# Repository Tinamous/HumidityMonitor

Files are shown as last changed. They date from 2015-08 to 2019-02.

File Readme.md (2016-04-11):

3D Printer Filament Humidity Controlled Storage
===============================================

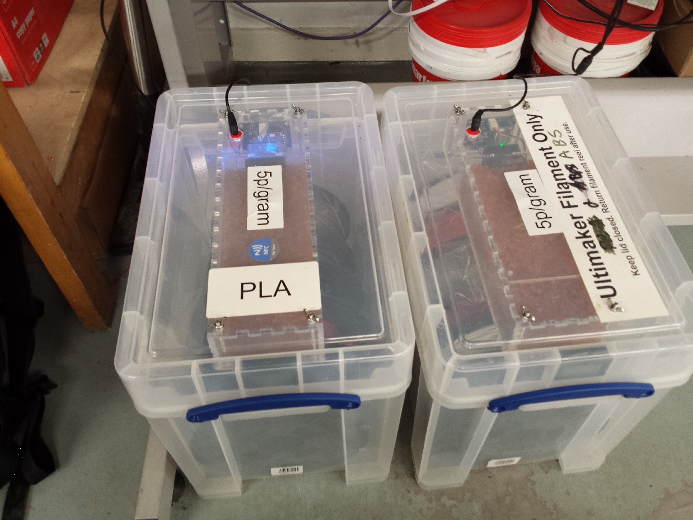
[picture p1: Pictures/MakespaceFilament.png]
Filament storage boxes in use


Comprises of:

* Outer box (19L XL Really Useful Box).
* Laser cut acrylic silica gel case
* Particle Photon based humidity sensing and fan control PCB inside silica gel case.
* Self indicating silica gel inside #2.

1) Outer box
---------------------
A 19L XL A4 suspension folder Really Useful Box works well. Be sure to get the one with the high lid. (not the regular 19L box).

* Needed: Staples link to case.
* Maplin: http://www.maplin.co.uk/p/really-useful-19l-xl-box-n68fl (Untested but it's a lot cheaper than the staples one!)

The lid of the 19L XL case will need to be drilled to hold the acrylic silica gel cartridge in place. Do this before gluing the cartridge so the acrylic can be used as a template.

Place what is labeled as the top piece in the designs (actually the bottom piece with all the holes in it) onto the lid and mark/drill the 4 corner screws.

If you wish for the power to go in via the top (prevents boxes being stacked but is obvious that it is powered so prevents people missing it) use the large bottom piece (actually top) with the larger round hole in it and align the two corner screws then drill out the larger hole in the lid.

Power connectors were sourced from eBay (http://www.ebay.co.uk/itm/PLUGZ2GO-2-1MM-X-5-5MM-PANEL-MOUNT-DC-PLUG-SOCKET-JACK-CHOICE-OF-COLOUR-/221456273750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), be sure you can get the same before drilling the power connector hole in the lid. 

Alternativly power connection may be done from the side of the lid by running the power cable out of either top or bottom gel case holes, this would allow the boxes to be stacked, although it makes it less obvious theirs a cable connected so care needs to be taken.

M4 x 70mm machine screws with washer+wingnut on the lit are used to hold the actylic case to the lid. (See notes below on re-filling the silica gel)

2) Laser Cut Acrylic Gel Case
-----------------------------
5mm clear acrylic cut as detailed in Hardware\Case\LaserCut

(You can use another colour obviously but the clear is cheaper and allows the self indicating gel to be seen).

The case contains a 40mm fan. A standard 3 pin PC fan should be used with a filter to prevent silica gel getting in to it.

3) Humidity Monitor.
---------------------

Use Particle Photon (or can use Particle Core device).

See Hardware\PCB\V2

Don't use V1 as the FET has Source/Drain the wrong way around.

PCB available from OSHPark: https://oshpark.com/shared_projects/nOVDuNCE

JP3 or JP4 are used for the HTU21 sensor. SparkFun and eBay boards have swapped SDA/SCL, watch for correct version.
* JP3 is for the eBay version
* JP4 is for SparkFun version.

Build using build.particle.io, see source folder.

A 12V power supply us needed capable of supplying upto 500mA (depends on the fan).

If a 5V fan is used a 5V PSU can be used and the onboard regulator not fitted, instead connecting the Vin to VOut holes with a piece of wire.

The PCB is mounted to the case with 4x 10mm plastic standoffs and 8x M3x8mm bolts from either side.

4) Self indicating silica gel
-----------------------------
Almost any silica gel can be used and doesn't need to be self indicating but it helps with seeing when the gel needs to be dried and when drying the gel that it is ready.

Gel should be stored in a sealed box/bag when not in use.

Gel can be re-generated by heating in an electric (untested on gas) oven for about 3 hours at 110°C

5) Connection to Tinamous
-------------------------
Optional step. Tinamous supports Particle devices by use of the ParticleBot in Tinamous and will automatically bring in and store devices/measurements so the humidity can be remotely monitored.

PLA Filament storage 24 hour humdity chart:

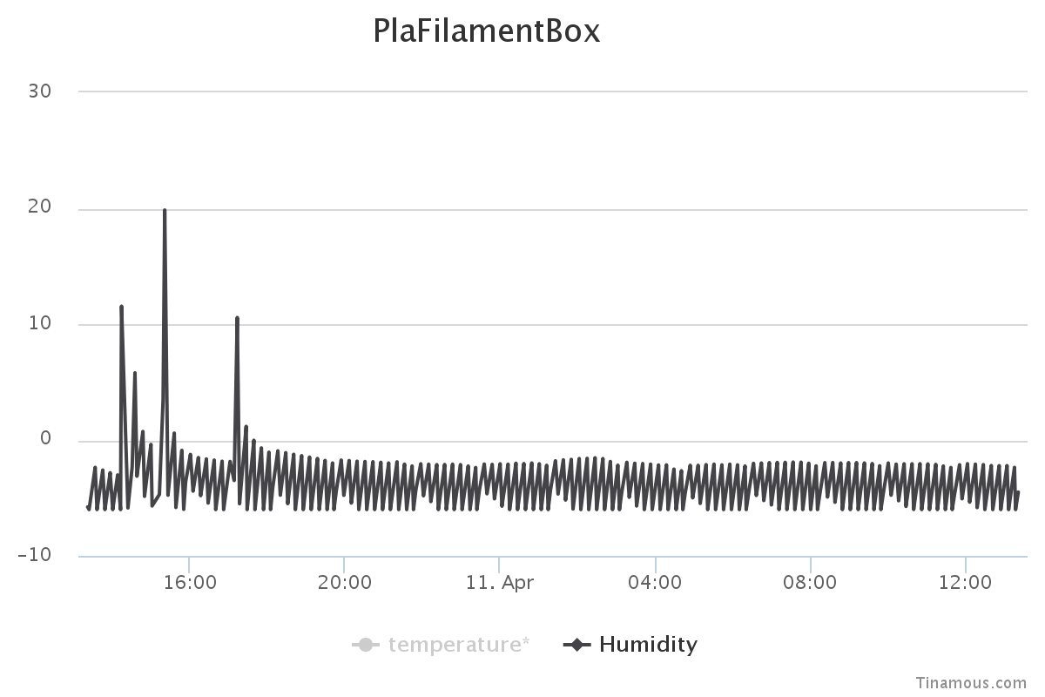
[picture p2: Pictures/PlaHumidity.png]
Humidity last 24 hours


PLA Filament storage 7 day humidity chart with change of gel:

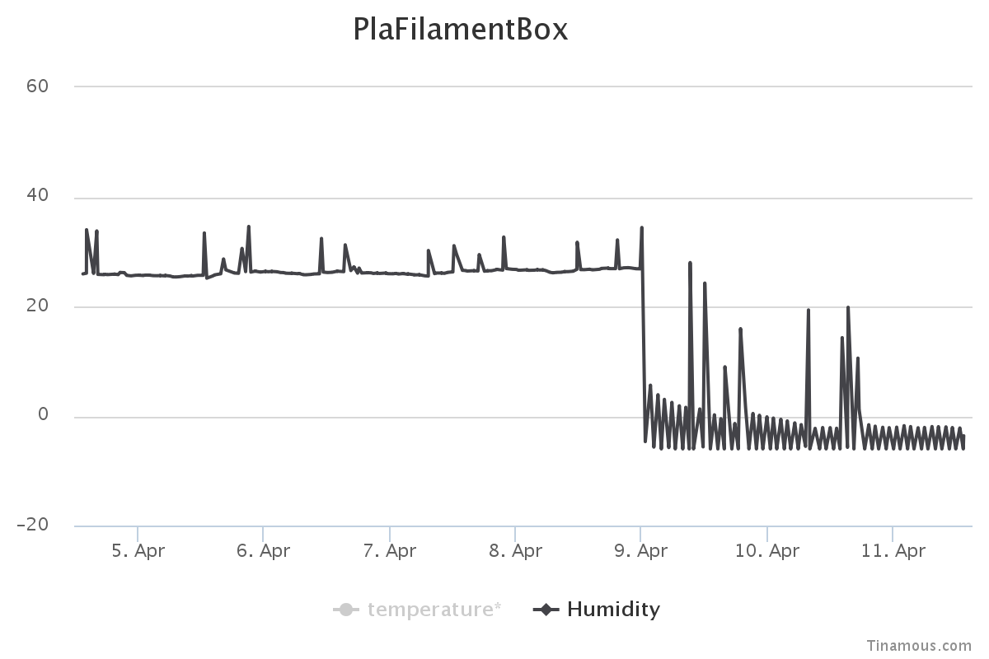
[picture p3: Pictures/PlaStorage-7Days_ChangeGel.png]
Humidity last 7 days


Notes
=====

Replacing the silica gel.
--------------------------

This needs to be done regularly (depending on usage), ca. every month and the silica gel dried (110C 3hrs spread out on a baking tray). I typically replace when it gets to about 20% humidity in the box.

The silica gel can be dried and re-used.

Silica gel will try to go everywhere.

* Remove acrylic case from box lid (place on flat surface, undo wing nuts on top of box.
* Remove lid upwards leaving acrylic case on flat surface.
* Replace 2x win nuts onto acrylic case at PCB end to hold the large top piece in place
* Remove small top piece from top to expose silica gel
* Remove 2x screws that were holding the top peice in
** failure to remove these now will result in silica gel getting wedged behind them and stopping correct alignment.
* Pour gel into a container (suggest Sistem 2.35L tub - http://www.amazon.co.uk/gp/product/B005D6Y4IA?psc=1&redirect=true&ref_=oh_aui_detailpage_o03_s00)
* Put funnel into opening
* Slowly pour fresh silica gel into acrylic case, shaking to move the gel down the case as you go
* Do not fill completly full, allow 1/2-1 inch space when the case is closed up and stood tall 
* Re-Fit small lid peiece
* Holding top in place, stand case tall to allow silica gel to fully move down to the fan and make re-fitting screws easier.
* Refit 2x screws for the small lid piece.
* Stand back down, remove 2x wingnuts to allow lit to be fitted.
* Fit box lit and re-fit wing nuts.

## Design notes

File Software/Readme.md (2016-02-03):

Humidity Monitor Source
-----------------------

Build and deployed using build.particle.io

If you paste this into a new file at build.particle.io you will need to manually add the HTU21D library (from the libraries tab).

Watch for the hardware version used. You should be using 0.2 PCB (i.e. Version 2), ensure version 1 pin assignments are commented out.

This application publishes senml messages which are automatically picked up by Tinamous.com to record the humidity/temperature levels and Status messages which show on the timeline.

Note that setting a new fan humidity trigger level using setFanOnAt method (which sets fanOnAtHumidityLevel) remotely does not persist this, it will be lost on power cycle/reset.

The application monitors the humidity level and will run the fan as needed.
* Either every n seconds (10s loop * 60, fan runs for 120s).
* When humidity > fanOnAtHumidityLevel (20%) and < 40% - fan will run for 120s or as long as the humidity level remains in this zone.
* If humidity level > 40% the fan is stopped to prevent flooding the silica gel with moisture (it is assumed to be in open air).

The Photon has a RGB LED on top, the color or this is used to indicate humidity levels
* Red - Humidity > 30%
* Yellow - Humidity > 20%
* Green - Humidity <= 20%

The fan can be remotely controlled via the Particle API (and via Tinamous) using:
* fanOn - runs the fan for 10 minutes
* fanOff - stops the fan within 10 seconds

No power saving is attempted with this version. A 10 second delay happens every loop which would be a good time to switch the WiFi off, however this makes updating and controlling the unit difficult and as it uses external power their is little need for power saving.

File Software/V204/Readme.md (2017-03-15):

Humidity Monitor Source
-----------------------

Build and deployed using build.particle.io

Paste the code from Humidityv4.ino into a new file at build.particle.io you will need to manually add the HTU21D library (from the libraries tab).

This works with the V2.04 PCB

This application publishes senml messages which are automatically picked up by Tinamous.com to record the humidity/temperature levels and Status messages which show on the timeline.

The application monitors the humidity level and will run the fan as needed.
* Either every n seconds (10s loop * 60, fan runs for 20s).
* When humidity > fanOnAtHumidityLevel (20%) and < humidityWarningLevel (30%) - fan will run for 60s or as long as the humidity level remains in this zone.
* If humidity level > humidityWarningLevel (30%) the fan is stopped and the beeper sounded to prevent flooding the silica gel with moisture (it is assumed to be in open air).

The Photon has a RGB LED on top, the color or this is used to indicate humidity levels
* Red - Humidity > 30%
* Yellow - Humidity > 20%
* Green - Humidity <= 20%

The fan can be remotely controlled via the Particle API (and via Tinamous) using:
* fanOn - runs the fan for 10 minutes
* fanOff - stops the fan within 10 seconds

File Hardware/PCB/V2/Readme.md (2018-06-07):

Filament Box IoT Humidity Sense and Control
---------------------------------------------

Used to monitor the humidity level in a 3D filament storage box and re-circulate the air through a silica gel cartridge.

Notes:
* 7805 Regulator should be replaces with a switching "780x replacement" type device to keep heat down. The 7805 will get very hot dropping 12v to 5v.
* JP3 and 4 are variants of connectors for HTU21D breakout boards.
** JP4 should be used with the Spark Fun version (https://www.sparkfun.com/products/12064)
** JP3 should be used with the common eBay version (SDA/SCL swapped from Spark Fun version).
* Normal use is intended for 12V with a 12V fan. However if using a 5V fan the supply may be dropped to 5V and IC1 (7805) not fitted, instead pads 1 & 3 connected to feed 5V directly into the photo's 5V supply pin.
* Do not use photon USB B connector to provide 5V for fan, it will not supply the full 5v and may not have PCB traces strong enough for the fan current.

Untested at this time. Awaiting PCBs.

BOM:

All 0805 unless specified

F1 - Fuse Farnell 1822224

D1,D2 - IN4148W (2x)
D4 - MBRA140
D3 - Green Reverse LED
D7 - Red Reverse LED
D8 - Yellow Reverse LED

R1,R2 - 10k (2x)
R3 - 100k
R4 - 180R
R5,R6,R7 - 1k5 (3x)

Q1 - BC817
Q2 - NXP2301

C1 - 1.0uF 
C4 - 0.1 25V
C2,C5 - 0.1uF (x)

SG1 - Buzzer (Farnell: 2098836)

JP1 - 2 Pin Molex + Header + 2.1MM DC Jack 973-1148
JP2 - 3 Pin Moxel + 3 wire 40mm fan 9731156

IC1 - 7805 equivelant
JP3 - HTU21D equv
U3 - Photon (needs 2x 18Pin headers)

PCB Spacers (4x)
M3 Machine Screws (8x)

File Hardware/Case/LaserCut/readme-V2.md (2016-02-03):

This is a case for silica gel that is inside the filament case. 

It is powered to monitor the humidity level and to run a fan forcing the humid air over the silica gel which greatly improves the reduction in humidity.

All measurements are in mm and from outside edges.

Case designed with http://www.makercase.com/

Files:
* GelCase-V2.02.svg - master svg as generated by MakerCase. Do not use for cutting
* GelCase-V2.02.json - master MakerCase model.
* Sheet-1-V2.02 - Cutting.svg - svg used to generate dxf for cutting. Has better layout. Cut from 600mm x 400mm x 5mm acrylic.
* FanInsert-V2.02.svg - the fan insert to fit cutouts defined in the gel case. This holds a 40mm fan. Fan needs filter to prevent inflow of silica gel.

Use only these for cutting the acrylic.
* Sheet-1-V2.02 - Cutting.svg
* FanInsert-V2.02.svg

Notes:
* In MakerCase the top and bottom are transposed. This readme refers to "Bottom" and "Top" as they are references in MakerCase with (actually ...) added to point out the final 
* When loading the json file into MakerCase ("Load Model" button) the material thickness is not correctly reloaded - use "Custom Material Thickness" and set to 5mm.

Assembly:
*Case should be glued on all sides except 
** The bottom (actually top) - the 2 part long piece with round power hole and 6 mounting holes.
** The fan insert
* Tensol 12 should be used for gluing the acrylic.
* Refrigerate glue for 12 hours before use.
* Remove protective cover fom acrylic for all except the bottom (aka top).
* Use electrical tape to hold the pieces together when gluing.
* Allow 3-4 hours for the glue to set (watch for glue leaking through joint - clean up as needed - don't rest on paper towels as it sticks)
* You may wish to fit the bottom (aka top) whilst the glue sets to help keep the case square but be careful it isn't glued inadvertantly via the glue up the sides

Dimensions
-----------

Outside:
--------
Height: 60 
Width: 100
Length: 300

Top (actually bottom):
------

Vent holes.

x 10 to 90 every 10mm
y 90 to 290 every 10mm

Large air intake:
* 15,20 -> 85,70 (70x50 mm) (buts up to fan mount

Top/Bottom connector mounts

M4 holes. 8mm support for 3mm screw.
8/2 = 4mm offset for center.
12 mm from each corner.

* M4 10,10
* M4 90,10
- first section
* M4 10,240
* M4 90,240

* M4 10,290
* M4 90,290

Bottom (actually top):
-------
Do not glue to rest of cased. It is removable to allow PCB to be accessed and gel to be replaced.

Helpd in place by screws to fan assembly and side moning screws.

Holes to align with top holes for fan/PCB enclosure.

- first secotion
* M4 10,290
* M4 90,290
* M4 10,60
* M4 90,60
- second section
* M4 10,10
* M4 90,10

M4 - Fan case (Not used)
* 19,345 - 20
* 81,345 - 20
* 19,345 - 102,
* 81,345 - 102

{"params":[19,20,4,5],"type":"roundHole"},
{"params":[81,20,4,6],"type":"roundHole"},
{"params":[81,102,4,7],"type":"roundHole"},
{"params":[19,102,4,8],"type":"roundHole"},

Back:
-------
PCB mount:
* M4 @ 24,11
* M4 @ 24,49
* M4 @ 76,11
* M4 @ 76,49

Extra:
-------

Cut line at 245mm in bottom to allow small segment to be removed for easier emptying.

** Holes in tabs to allow for fixing of top and lower segment.

Internal partition
-------------------

M4 - Fan mount.
x,y,size, index
* {"params":[66,29,4,1],"type":"roundHole"},
* {"params":[34,29,4,2],"type":"roundHole"},
* {"params":[66,61,4,3],"type":"roundHole"},
* {"params":[34,61,4,4],"type":"roundHole"},

M4 - Fan case
* 19, 20
* 81,20
* 19,102,
* 81,102

{"params":[19,20,4,5],"type":"roundHole"},
{"params":[81,20,4,6],"type":"roundHole"},
{"params":[81,102,4,7],"type":"roundHole"},
{"params":[19,102,4,8],"type":"roundHole"},

// @ 25,95 25mm x 10mm - humidity sensor + power
{"params":[25,95,25, 25,10,9],"type":"rectHole"},

Fan
* {"params":[50,55,38,27],"type":"roundHole"}],

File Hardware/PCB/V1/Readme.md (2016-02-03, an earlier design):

Version 1 Design.

Note that the Q1 has Source and Drain pins the wrong way around. When fitting Q1 rotate it 180 degrees and shift right so that the gate pin is not over a hole and on the right hand side.

Connect a wire between gate and the left most hole for Q1 (from above with the photon on the right). remaining 2 pins go into the remaining holes.

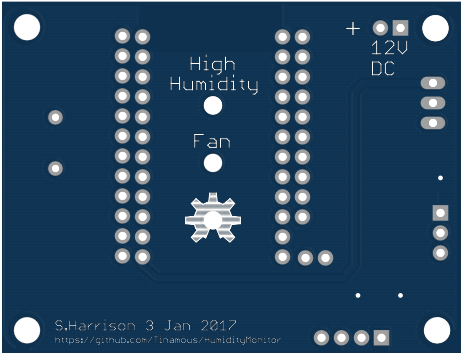
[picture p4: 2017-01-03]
Hardware/PCB/V2/Images/PcbBottom-V2.04.png

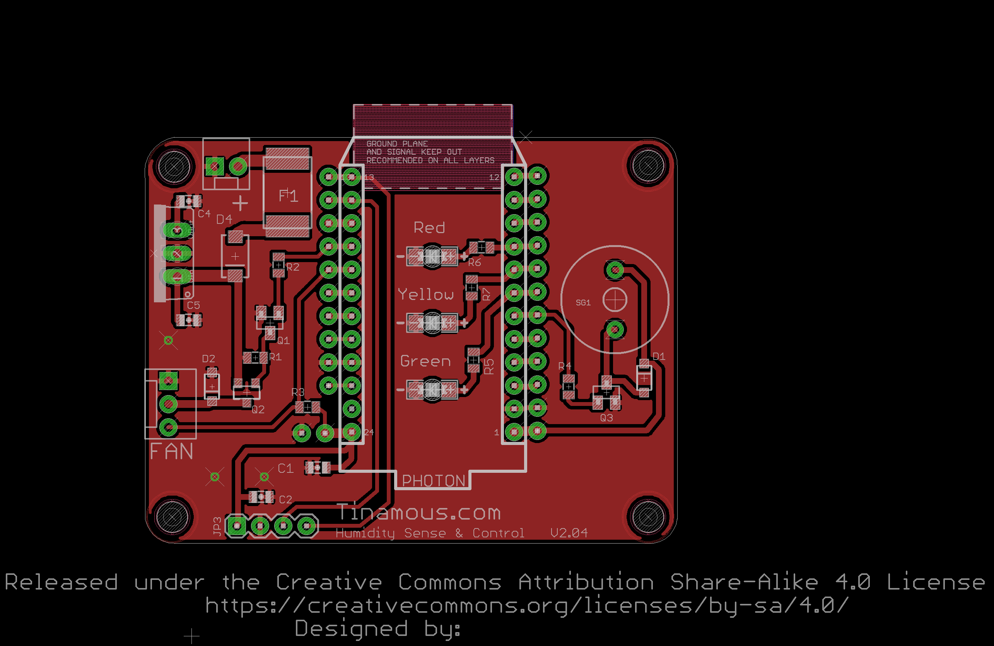
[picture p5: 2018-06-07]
Hardware/PCB/V2/Images/PcbTop-Design-V2.04.png

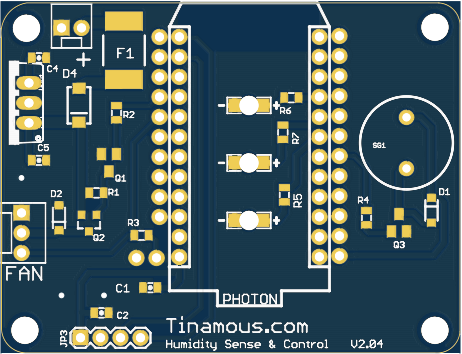
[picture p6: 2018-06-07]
Hardware/PCB/V2/Images/PcbTop-V2.04b.png

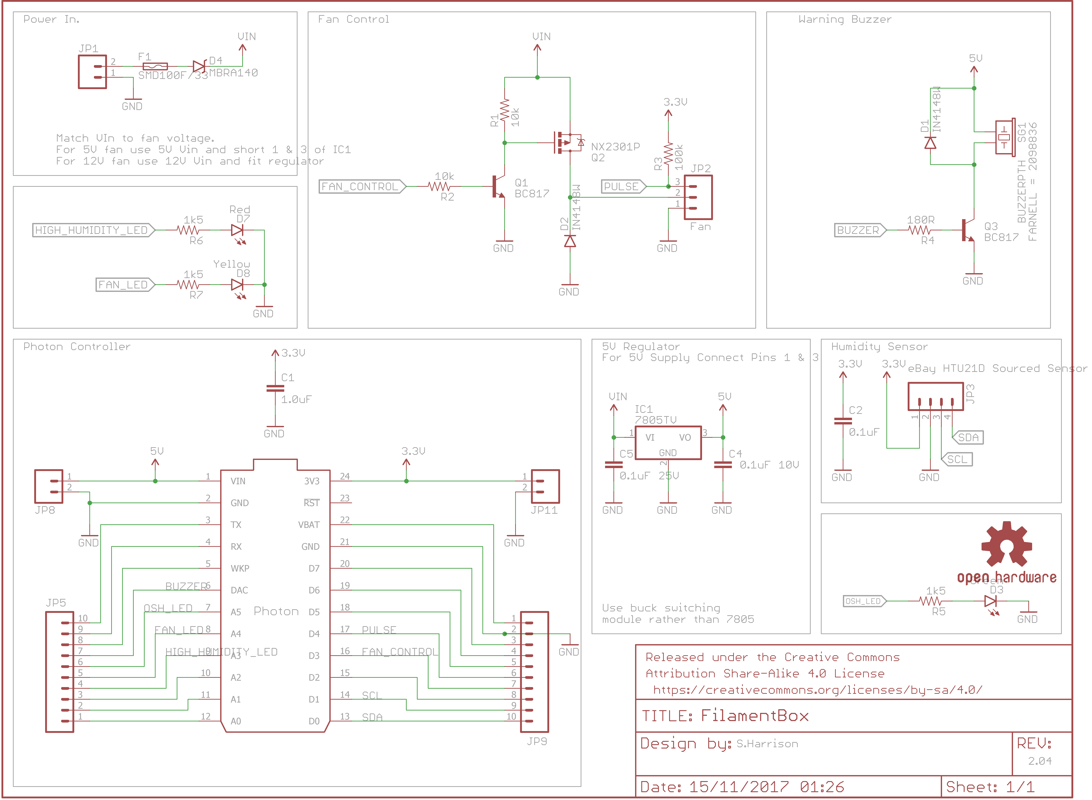
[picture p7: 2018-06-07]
Hardware/PCB/V2/Images/Schematic-V2.04.png

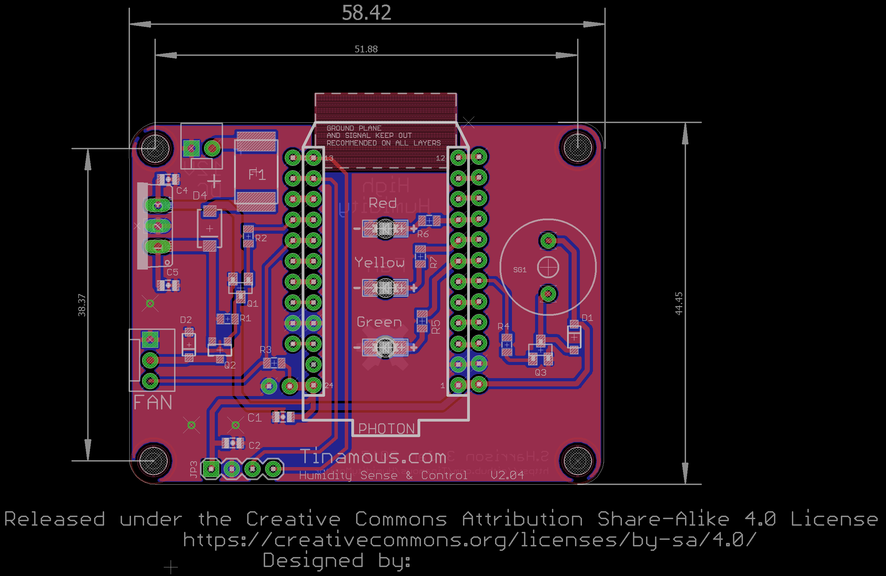
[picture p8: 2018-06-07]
Hardware/PCB/V2/Images/PCBAll-V2.04.png

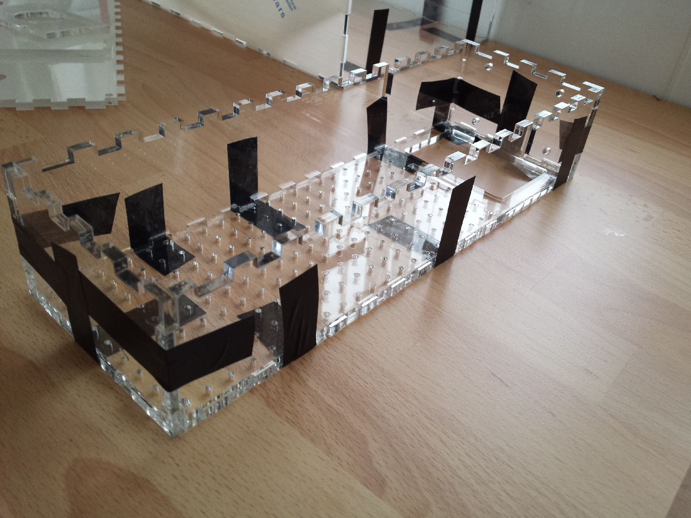
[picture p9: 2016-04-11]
Pictures/Gluing3.png

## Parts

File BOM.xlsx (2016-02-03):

Component | Part | Size/Value | Qty | Part Number(s) | Supplier | Supplier Part | Cost | Alt. Supplier | Alt. Supplier Part | Notes
Overall:
 | Really Useful Box | 19L XL | 1 |  | Staples | http://www.staples.co.uk/plastic-storage/cbs/431832.html?promoCode=200200555&Effort_Code=WW&Find_Number=431832 | 17.99 | Maplin | http://www.maplin.co.uk/p/really-useful-19l-xl-box-n68fl
 | Sistem tub | 2.35L | 1 |  | Amazon.co.uk | http://www.amazon.co.uk/gp/product/B005D6Y4IA?psc=1&redirect=true&ref_=oh_aui_detailpage_o03_s00 | 5.5 |  |  | Unused gel storage
 | 12V PSU |  | 1 |  | Maplin | N93JU | 9.99 |  |  | http://www.maplin.co.uk/p/12v-500ma-acdc-power-supply-n93ju
 | Machine Screw | M4 x 70mm | 4 |  | Westfield Fastners | http://www.westfieldfasteners.co.uk/A2_ScrewBolt_PoziPan_M4.html | 2.47
 | Wing nut | M4 | 4 |  | Westfield Fastners | http://www.westfieldfasteners.co.uk/A2_Nut_M4.html | 3.29
 | Draft Excluder |  | 1pk |  | B&Q |  |  | Wickes
 | Fan | 40mm | 1 |  | Maplin | N86QQ | 5 | http://www.maplin.co.uk/p/40mm-brushless-12vdc-axial-fan-yz41u
 | Fan filter | 40mm | 1 |  | eBay | http://www.ebay.co.uk/itm/like/291536178882 | 1.73
 | Silica Gel | 1kg | 1 |  | eBay | http://www.ebay.co.uk/itm/1000g-1kg-BONUS-100g-BAG-Silica-Gel-Desiccant-Self-Indicating-Loose-/111737656127 | 8.95
 | M3 Bolts | M3 x 25mm | 4 |  |  |  |  |  |  | Select length based on fan depth + 5mm + grill
 | M3 Nuts | M3 | 4
Acrylic Case: |  |  | QTY
 | Acrylic Sheet | 600x400x5mm | 1 |  | http://plasticonline.co.uk/ | http://plasticonline.co.uk/acrylic/acrylic-sheets-1/clear-cast-acrylic-sheet-gs.html | 10.43 |  |  | Clear Cast Acrylic Sheet (GS) - 5mm - 600x400
 | Glue - Tensol 12 | 50ml | 1 |  |  | http://www.ebay.co.uk/itm/50ml-TENSOL-12-Bottle-ACRYLIC-Perspex-Bonding-Cement-Adhesive-Glue-/160652606560 | 5.35
PCB:
 | PCB |  |  | 1 | OSH Park | https://oshpark.com/shared_projects/nOVDuNCE | 15 |  |  | USD 20 - for 3.
 | Photon | With Headers |  | U3 | Particle | https://store.particle.io/collections/photon | 19.98 | CoolComponents.co.uk | https://www.coolcomponents.co.uk/photon-wi-fi-development-board.html
 | Photon Socket | 12Pin | 2 | U3 (Optional) | eBay | http://www.ebay.co.uk/itm/350800310361 | 1.69 |  |  | 2.54mm Single Row Female Pitch Header Socket Connector Pin Strip
 | Ceramic 0805 Cap | 0.1uF | 1 | C2 | Farnell | 1856422 | 0.04
 | Ceramic 0805 Cap | 1uF | 2 | C1,C4 | Farnell | 175-9422 | 0.066
 | Electrolytic - Through Hole | 10uF | 1 | C3 | Farnell
 | 5 V regulator (Use 7805 switching replacement) | 7805 | 1 | IC1 | eBay | http://www.ebay.co.uk/itm/331681032438 | 1.83
 | 2 Pin Molex 2.54mm pin | 2 pin | 1 | JP1 | Farnell | 9731148 | 0.084
 | 2 Pin Molex 2.54mm housing | 2 pin | 1 | JP1 | Farnell | 143126 | 0.135
 | Molex KK series crimp |  | 2 | JP1 | Farnell | 2424111 | 0.044 |  |  | Min. order 100
 | Thick film 0805 resistor | 10k | 2 | R1,R2 | Farnell
 | Thick film 0805 resistor | 100k | 1 | R3 | Farnell
 | BC817 Transistor (SOT23) | BC817 | 1 | Q1 | Farnell | 1081225 | 0.03
 | NX2301P P-Channel FET | NX2301P | 1 | Q2 | Farnell | 1894738 | 0.14
 | 3 Pin Molex 2.54mm | 3 Pin | 1 | JP2 | Farnell | 9731156 | 0.174
Do No Fit | Buzzer |  |  | SG1 | Farnell
Do No Fit | BC817 | BC817 | 1 | Q3 | Farnell | 1081225
Do No Fit | Thick film 0805 resistor | 180R | 1 | R4 | Farnell
 | HTU21D Breakout | HTU21D Breakout | 1 |  | eBay | http://www.ebay.co.uk/itm/1PC-NEW-HTU21D-Temperature-Humidity-Sensor-Breakout-Board-New-Module-/271969988766 | 1.5
 | 2.54mm pitch pins |  | 4 |  |  |  |  |  |  | To mount HTU21D board
 | Panel Socket | 2.1mmx5.5mm | 1 |  | eBay | http://www.ebay.co.uk/itm/221456273750 | 2.49 |  |  | For 2
 | PCB Mounts | M3x10mm | 4 |  | eBay
 | M3 Screws | M3x8mm | 8 |  | Farnell | 1419987 | 1.87 |  |  | For pk 100
Total Cost |  |  |  |  |  |  | 115.773

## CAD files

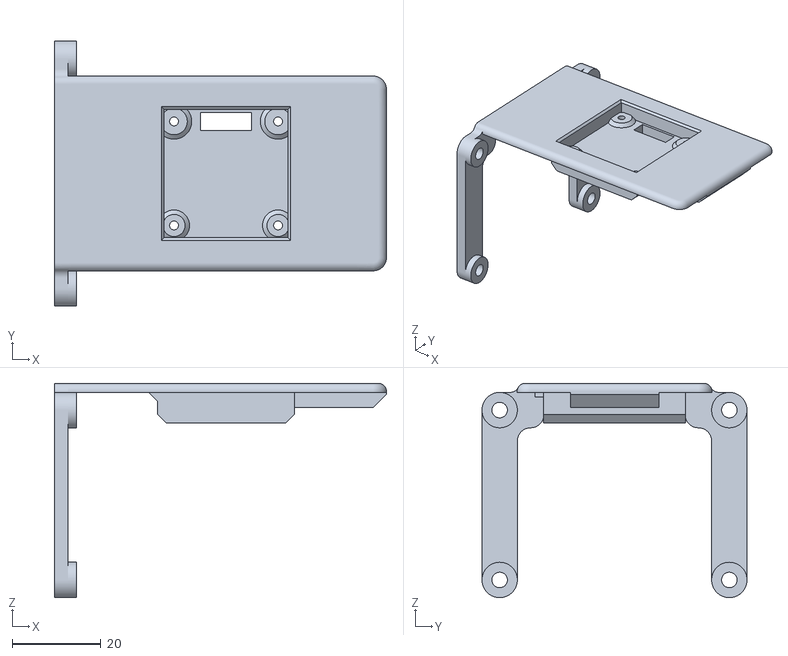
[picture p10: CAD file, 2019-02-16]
Hardware/Case/3D Printer/ScreehHolder2-4.stl
75.0 x 59.9 x 48.4

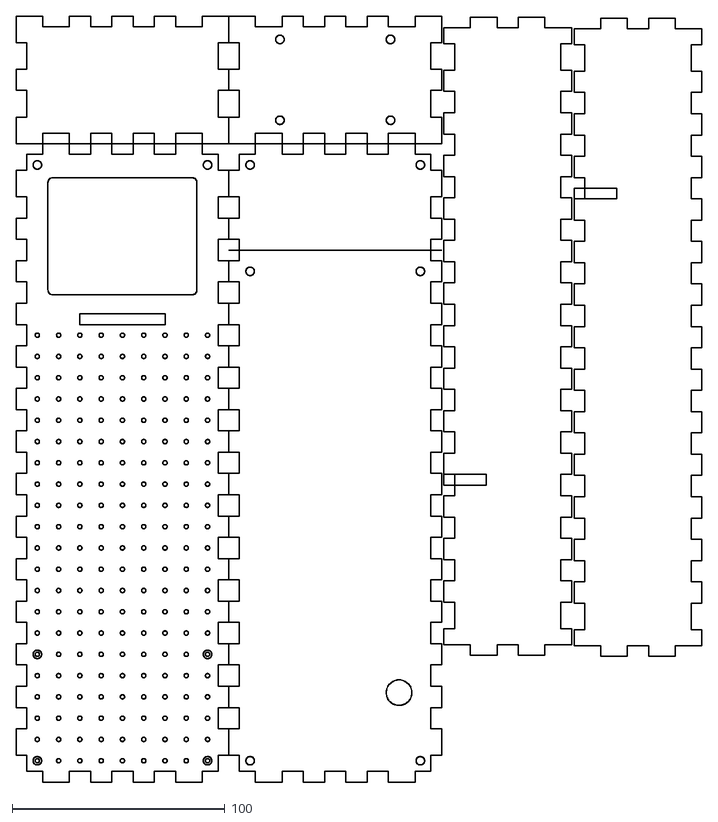
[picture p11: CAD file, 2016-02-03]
Hardware/Case/LaserCut/Sheet-1-V2.02 - Cutting.dxf
322.3 x 360.0

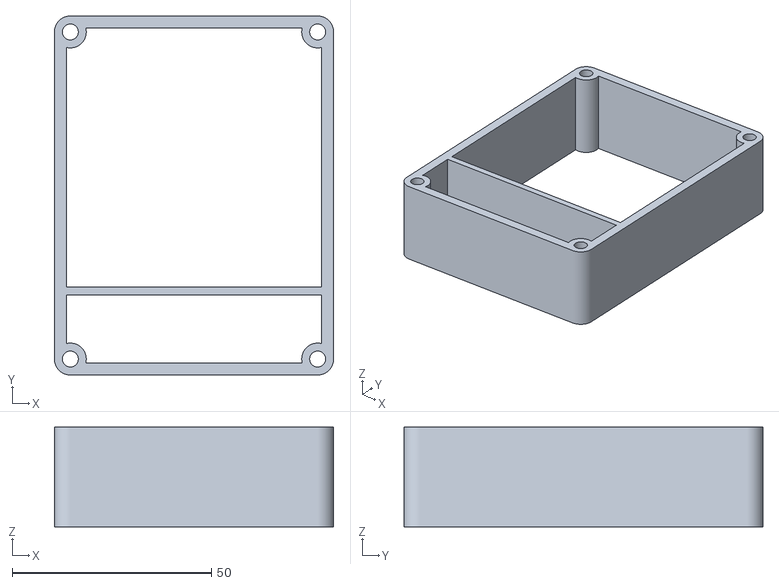
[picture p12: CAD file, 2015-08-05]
Hardware/Case/MiniGellBox/SilicaGelCase.stl
70.0 x 90.0 x 25.0

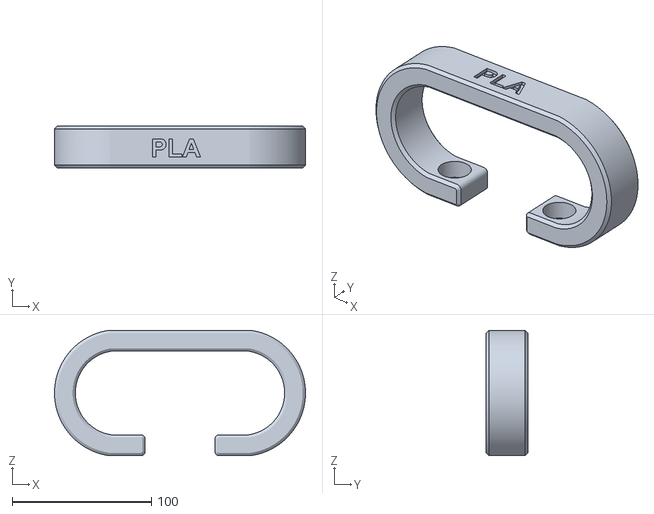
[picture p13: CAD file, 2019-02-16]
Hardware/Case/3D Printer/Handle3-PLA.stl
180.0 x 30.0 x 90.0

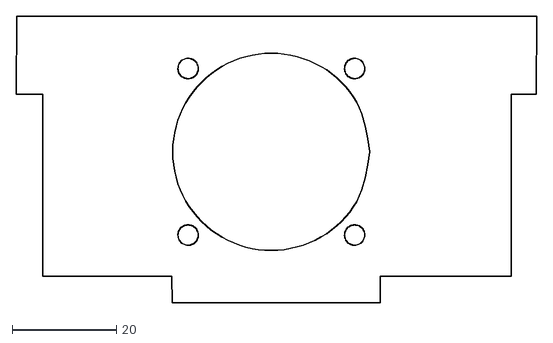
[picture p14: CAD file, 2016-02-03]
Hardware/Case/LaserCut/FanInsert-V2.02.dxf
100.0 x 55.1

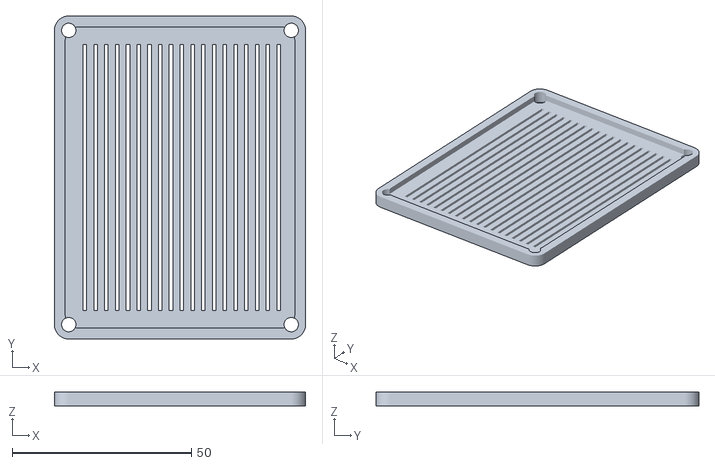
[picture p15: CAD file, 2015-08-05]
Hardware/Case/MiniGellBox/SilicaGelCaseLid.stl
70.0 x 90.0 x 4.00

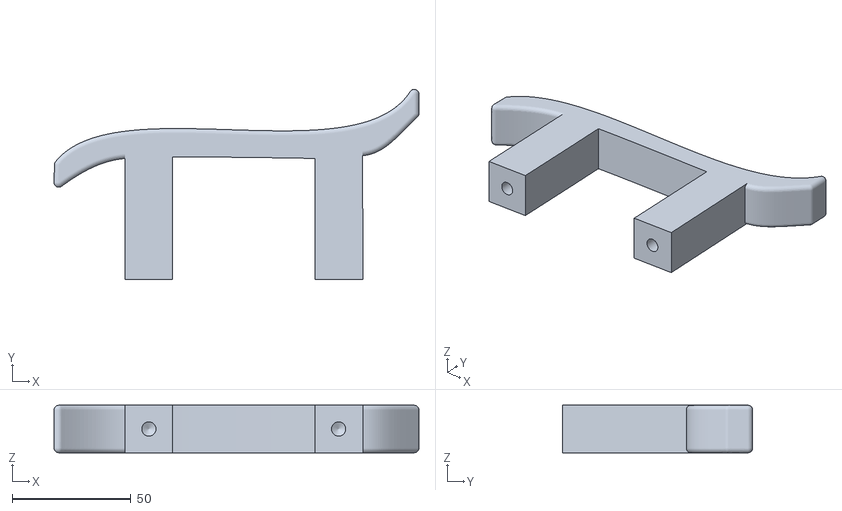
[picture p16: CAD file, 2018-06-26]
Hardware/Case/3D Printer/PiHandle.stl
153.5 x 80.1 x 20.0

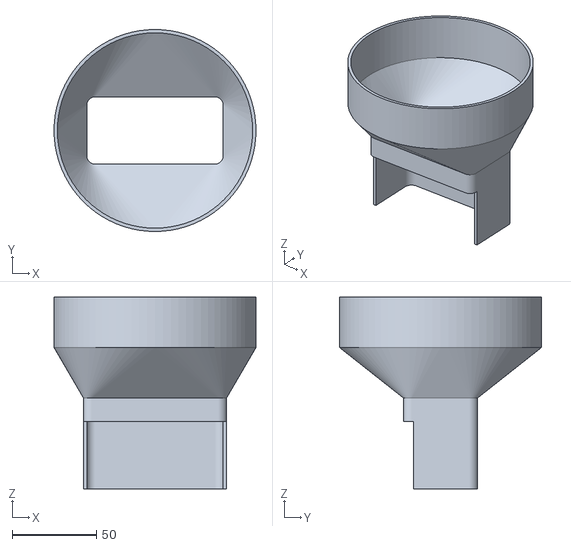
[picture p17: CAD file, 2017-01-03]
Hardware/Case/3D Printer/Funnel3.stl
120.0 x 120.0 x 114.0

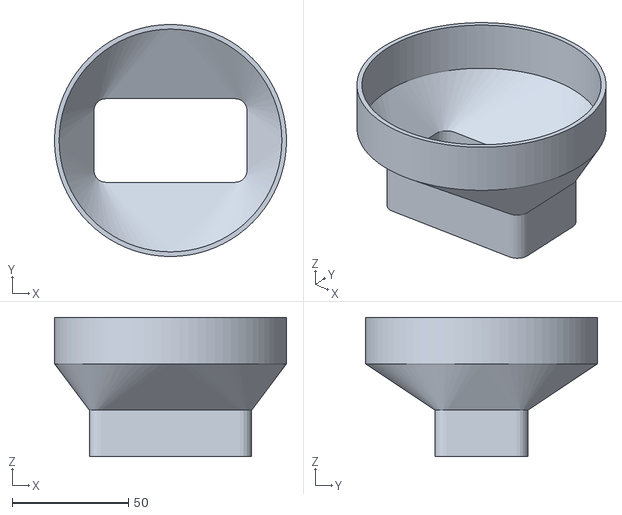
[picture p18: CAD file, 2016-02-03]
Hardware/Case/3D Printer/Funnel2.stl
100.0 x 100.0 x 60.0

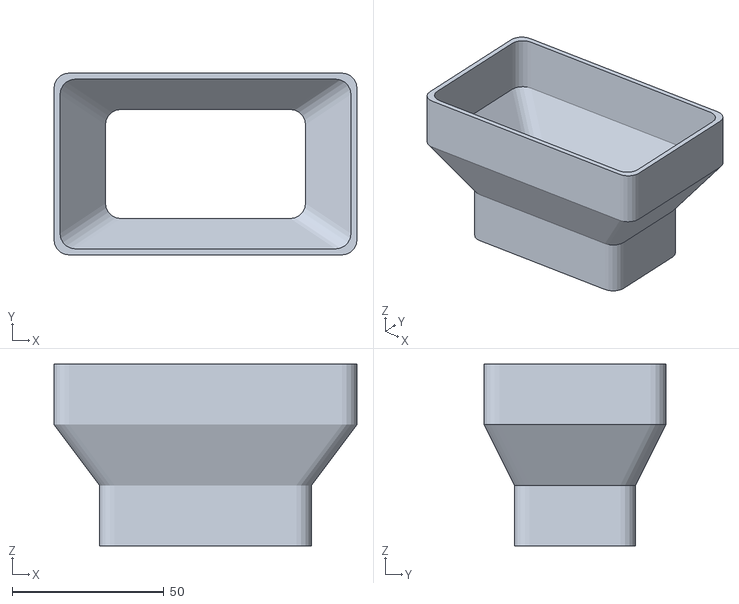
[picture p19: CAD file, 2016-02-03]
Hardware/Case/3D Printer/Funnel.stl
100.0 x 60.0 x 60.0

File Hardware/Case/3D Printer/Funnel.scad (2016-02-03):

radius = 5;
$fn=20;

// -----------------------------------------
// -----------------------------------------
module GenericBase(xDistance, yDistance, zHeight) {
	translate([radius,radius,0]) {
		minkowski()
		{
			cube([xDistance-(radius*2), yDistance-(radius*2), (zHeight/2)]);
			cylinder(r=radius,h=(zHeight/2));
		}
	}
}

module HollowGenericBase(xDistance, yDistance, zHeight) {
    difference() {
        union() {
            GenericBase(xDistance, yDistance, zHeight);
        }
        union() {
            translate([2,2,0]) {
                //GenericBase(xDistance-2, yDistance-2, zHeight);
            }
        }
    }
}

// -----------------------------------------
// -----------------------------------------
module Funnel(baseWidth, baseDepth, topWidth, topDepth) {
   
    GenericBase(baseWidth, baseDepth, 20);
       
    hull() {
       
        // box section
        translate([0,0,20]) {
        GenericBase(baseWidth, baseDepth, 20);
        }
                   
        // Top of the funnel
        translate([-((topWidth-baseWidth)/2),-((topDepth-baseDepth)/2),20+20]) {
            GenericBase(topWidth, topDepth, 20);
        }
    }
        
}

difference() {
    Funnel(70,40, 100, 60);
    translate([2,2,0]) {
        Funnel(70-4,40-4, 100-4, 60-4);
    }
}

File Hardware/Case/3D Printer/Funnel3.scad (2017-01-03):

radius = 5;
$fn=200;

// -----------------------------------------
// -----------------------------------------
module GenericBase(xDistance, yDistance, zHeight) {
	translate([radius,radius,0]) {
		minkowski()
		{
			cube([xDistance-(radius*2), yDistance-(radius*2), (zHeight/2)]);
			cylinder(r=radius,h=(zHeight/2));
		}
	}
}

module HollowGenericBase(xDistance, yDistance, zHeight) {
    difference() {
        union() {
            GenericBase(xDistance, yDistance, zHeight);
        }
        union() {
            translate([2,2,0]) {
                //GenericBase(xDistance-2, yDistance-2, zHeight);
            }
        }
    }
}

// -----------------------------------------
// -----------------------------------------
module Funnel(baseWidth, baseDepth, topWidth, topDepth) {
    
    
    baseToFunnelHullConnection = 1;
    baseBoxHeight = 55 - baseToFunnelHullConnection;
    funnelTopHeigth = 30;
    hullConnectionHeight = 30; //baseBoxHeight; //40;
   
    difference() {
        GenericBase(baseWidth, baseDepth, baseBoxHeight);
    }
       
    hull() {
       
        // box section
        translate([0,0,baseBoxHeight]) {
            // This connects the base box to the cylinder at the top through
            // the hull connection
            GenericBase(baseWidth, baseDepth, baseToFunnelHullConnection);
        }
        
        // Align the center of the base cube
        // With the center of the cylinder
        baseXCenter = baseWidth /2 ;
        baseYCenter = baseDepth / 2;
        
                   
        // Top of the funnel
        //translate([-((topWidth-baseWidth)/2),-((topDepth-baseDepth)/2),20+20]) {
        translate([baseXCenter,baseYCenter,hullConnectionHeight+baseBoxHeight]) {
            //GenericBase(topWidth, topDepth, 20);
            cylinder(d=topWidth, h=funnelTopHeigth, $fn=80);
        }
    }
        
}



wallThickness = 2;

baseWidth = 85; //70;
baseDepth = 44; //40;
topWidth = 120;
topDepth = 40;

difference() {
    
    // Funnel Outer
    // 100x44
    Funnel(baseWidth,baseDepth, topWidth, topDepth);
    
    union() {
    
        // Subtract the inner.
        translate([wallThickness,wallThickness,0]) {
            Funnel(baseWidth-(wallThickness*2),
                baseDepth-(wallThickness*2), 
                topWidth-(wallThickness*2), 
                topDepth-(wallThickness*2));
        }
        
        // Cut out a section so that the funnel
        // can sit and still allow stuff to flow out
        #cube([baseWidth,6,40]);
    }
}

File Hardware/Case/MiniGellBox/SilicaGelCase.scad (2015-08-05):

use <MCAD/boxes.scad>

// Overall size
height = 25;
length = 90;
width = 70;

outerWallWidth = 3;
radius = 4;
drillHoldRadius = 2; // 4mm Hole

// PCB Support goes vertical 
// on both long walls.
pcbSupportHeight = height;

// How far into the center the supports go.
// this wifth includes the wall width as well.
// so 6mm support gives actual 6-3 (outerWallWidth) = 3mm into box.
// width = 70.
// Arduino needs 52
// 9mm supports either size
pcbSupportWidth = 9; // 
pcbSupportLength = 6; //(6-pcbHeight)/2 gives size either size of PCB - about 2mm
pcbHeight = 2.0; // 1.6mm PCB

// PCB Max 62mm x 45mm max (x 1.6mm) - actual length of PCB
// Ardiono is 53.5 mm wide
// needs seperation between supports of 51-52mm
pcbWidth = 62; 
// Max pcbWidth is govened by the support height.
pcbYOffset = 20;
$fn=100;

// -----------------------------------------
// -----------------------------------------
module GenericBase(xDistance, yDistance, zHeight) {
    
// -----------------------------------------
// Show a fan box in the unit to give perspective
// -----------------------------------------
	//roundedBox([xDistance, yDistance, zHeight], 2, true);

	// Create a rectangluar base to work from that
	// is xDistance by yDistance and zHeight height.

	// This is effectivly a cube with rounded corners

	// extend the base out by 3.5 from holes by using minkowski
	// which gives rounded corners to the board in the process
	// matching the Gadgeteer design
	


	translate([radius,radius,0]) {
		minkowski()
		{
			cube([xDistance-(radius*2), yDistance-(radius*2), (zHeight/2)]);
			cylinder(r=radius,h=(zHeight/2));
		}
	}
}

// -----------------------------------------
// 
// -----------------------------------------
module MakeBox() {
    
    difference() {
        union() {
            GenericBase(width,length,height);
        }
        union() {
            translate([outerWallWidth,outerWallWidth,-2]) {
                GenericBase(width - (outerWallWidth*2),length  - (outerWallWidth*2),height+2);
            }
        }
    }
}

// -----------------------------------------
// Mounting posts
// -----------------------------------------
module Posts() {
    
   
    union() {
        translate([radius,radius,0]) {
            cylinder(h=height, r=radius,center=false);
        }
        translate([width-radius,length-radius,0]) {
            cylinder(h=height, r=radius,center=false);
        }
        translate([width-radius, radius,0]) {
            cylinder(h=height, r=radius,center=false);
        }
        translate([radius,length-radius,0]) {
            cylinder(h=height, r=radius,center=false);
        }
    }
}

// -----------------------------------------
// Create holes in posts for screws
// Using M3 inserts from InsertsDirect
// -----------------------------------------
module PostHoles() {
    union() {
            translate([radius,radius,-1]) {
                #cylinder(h=height+2, r=drillHoldRadius,center=false);
            }
            translate([width-radius,length-radius,-1]) {
                #cylinder(h=height+2, r=drillHoldRadius,center=false);
            }
            translate([width-radius, radius,-1]) {
                #cylinder(h=height+2, r=drillHoldRadius,center=false);
            }
            translate([radius,length-radius,-1]) {
                #cylinder(h=height+2, r=drillHoldRadius,center=false);
            }
        }
}

module AddSensorWall() {
    // Add compartment for sensor.
    translate([0, 20,0]) {
        cube([width, 2, height]);
    }
}

// -----------------------------------------
// -----------------------------------------
module Debug() {
    difference() {
    union() {
        MakeBox();
        AddSensorWall();
        Posts();
    }
    union() {
        PostHoles();
    }
}
}

// Comment out when building, uncomment for debug.
Debug();

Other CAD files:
Hardware/Case/3D Printer/Handle3-Makespace.stl
Hardware/Case/3D Printer/Handle3-TPU.stl
Hardware/Case/3D Printer/Handle3-ABS.stl
Hardware/Case/3D Printer/Funnel2.scad
Hardware/Case/MiniGellBox/SilicaGelCaseLid.scad

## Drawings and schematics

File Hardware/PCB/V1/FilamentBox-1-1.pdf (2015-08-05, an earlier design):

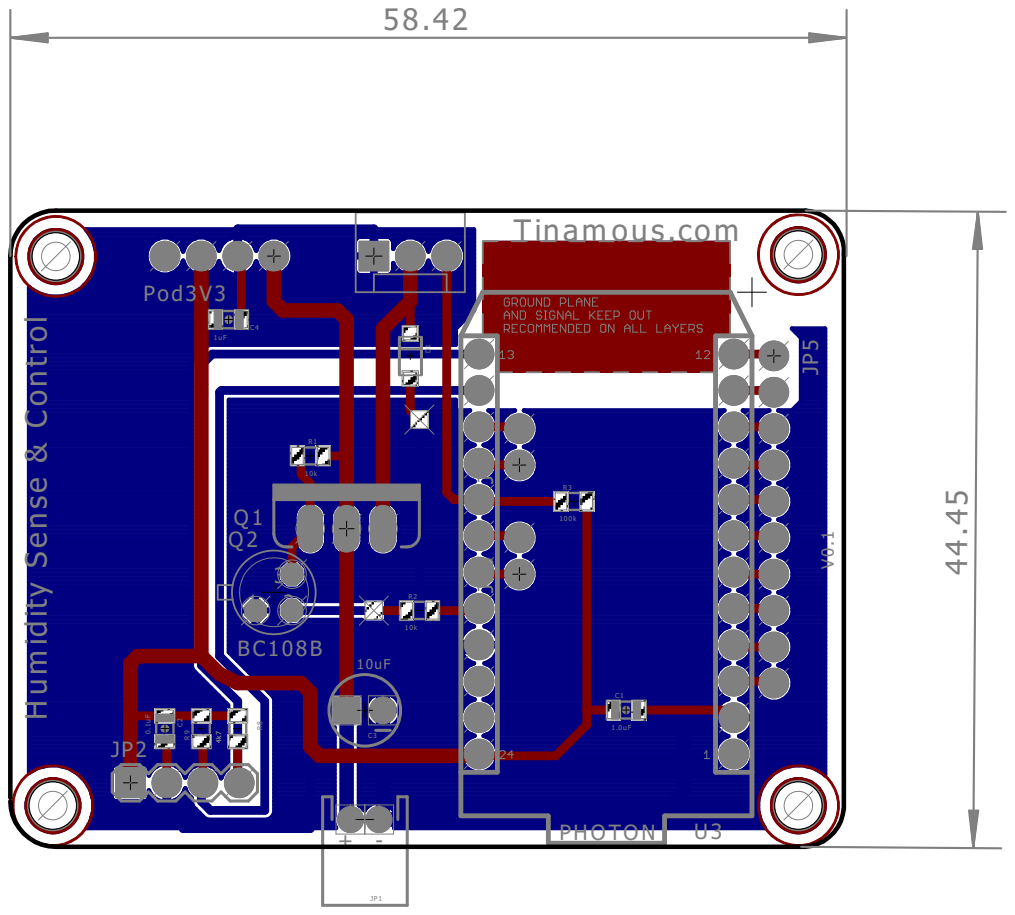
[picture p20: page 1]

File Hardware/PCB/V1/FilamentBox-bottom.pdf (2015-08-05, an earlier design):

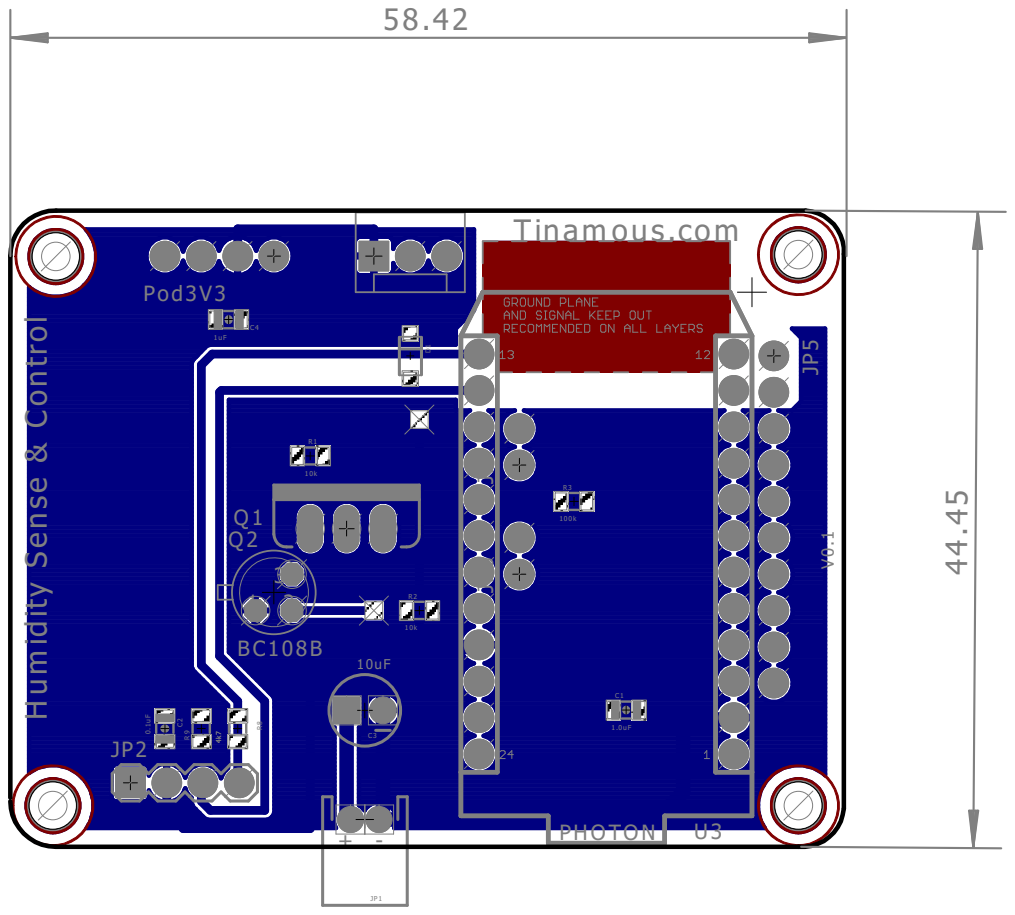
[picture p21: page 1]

R1 | 1.0uF 4k7 Pod3V3

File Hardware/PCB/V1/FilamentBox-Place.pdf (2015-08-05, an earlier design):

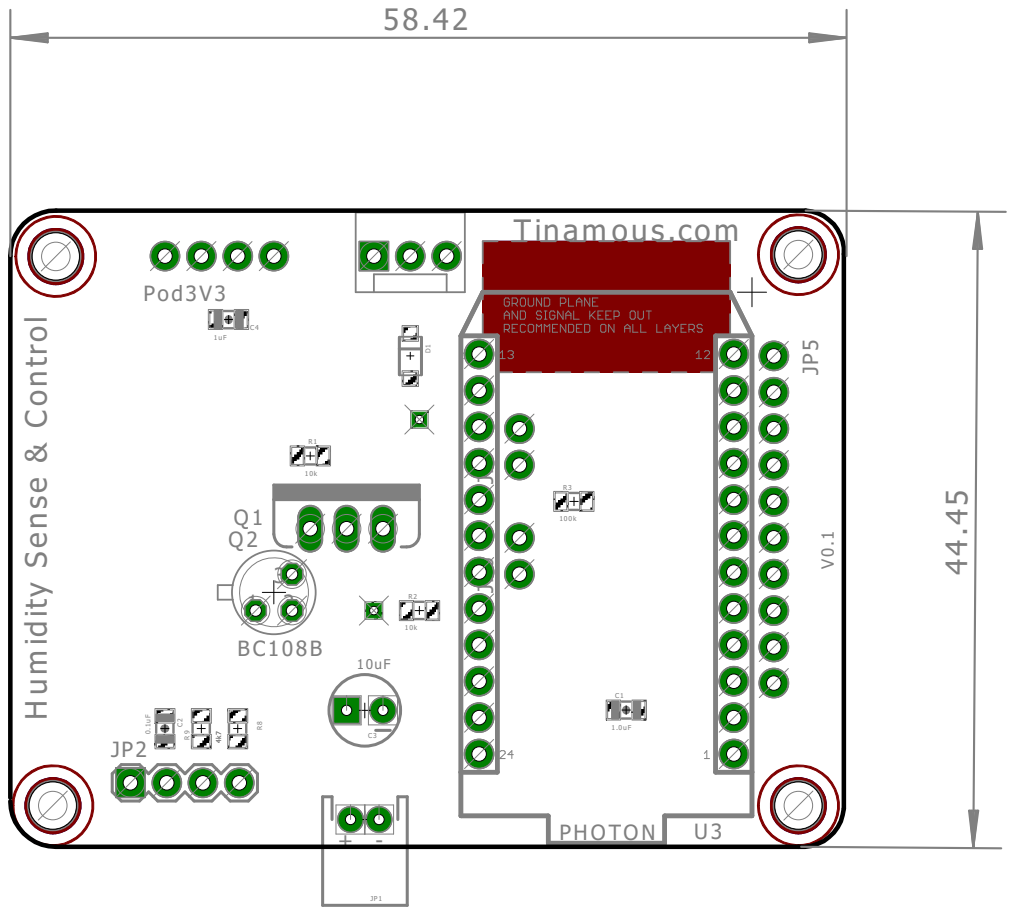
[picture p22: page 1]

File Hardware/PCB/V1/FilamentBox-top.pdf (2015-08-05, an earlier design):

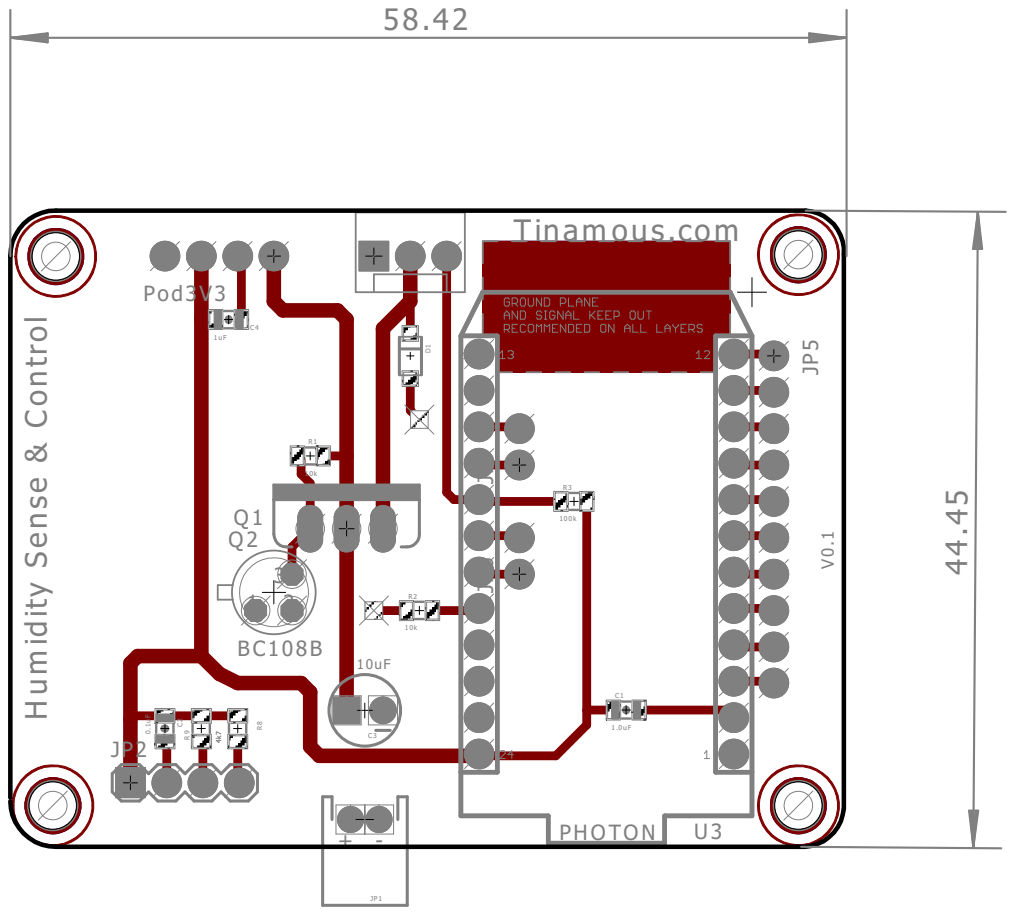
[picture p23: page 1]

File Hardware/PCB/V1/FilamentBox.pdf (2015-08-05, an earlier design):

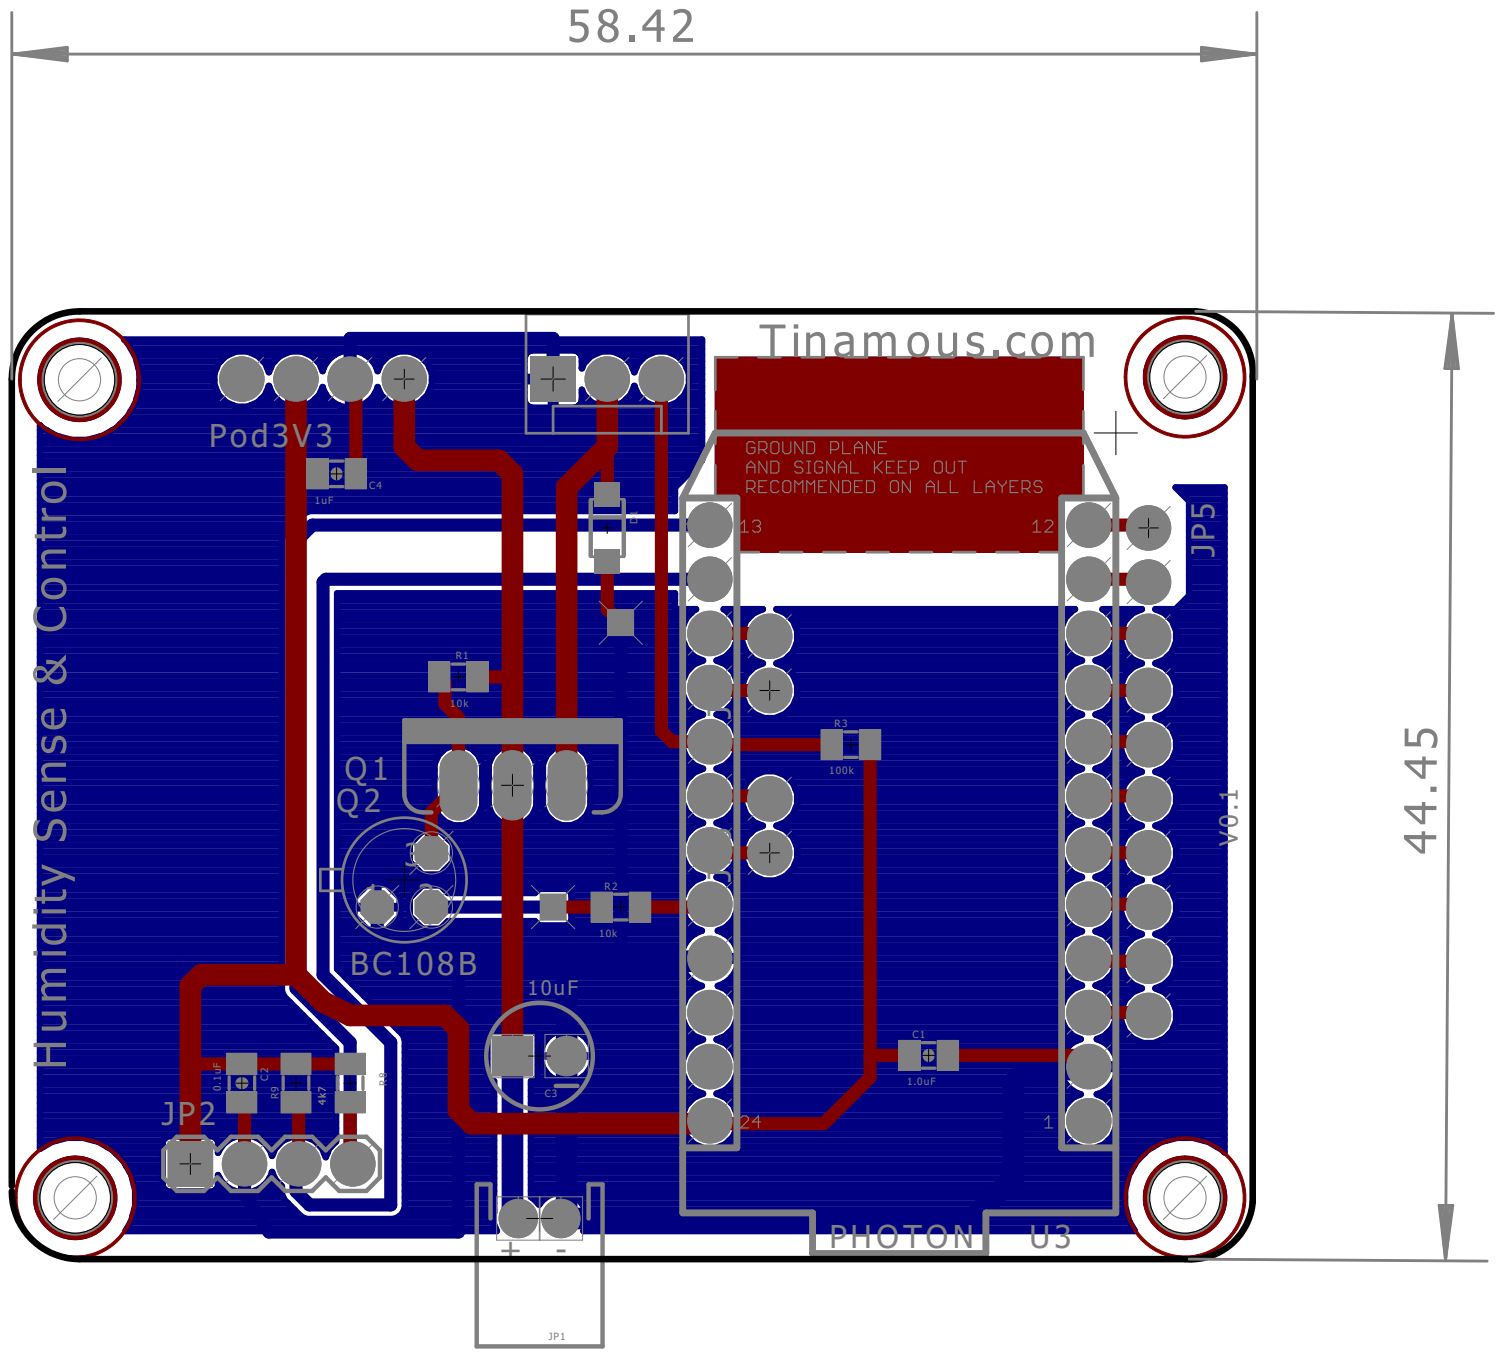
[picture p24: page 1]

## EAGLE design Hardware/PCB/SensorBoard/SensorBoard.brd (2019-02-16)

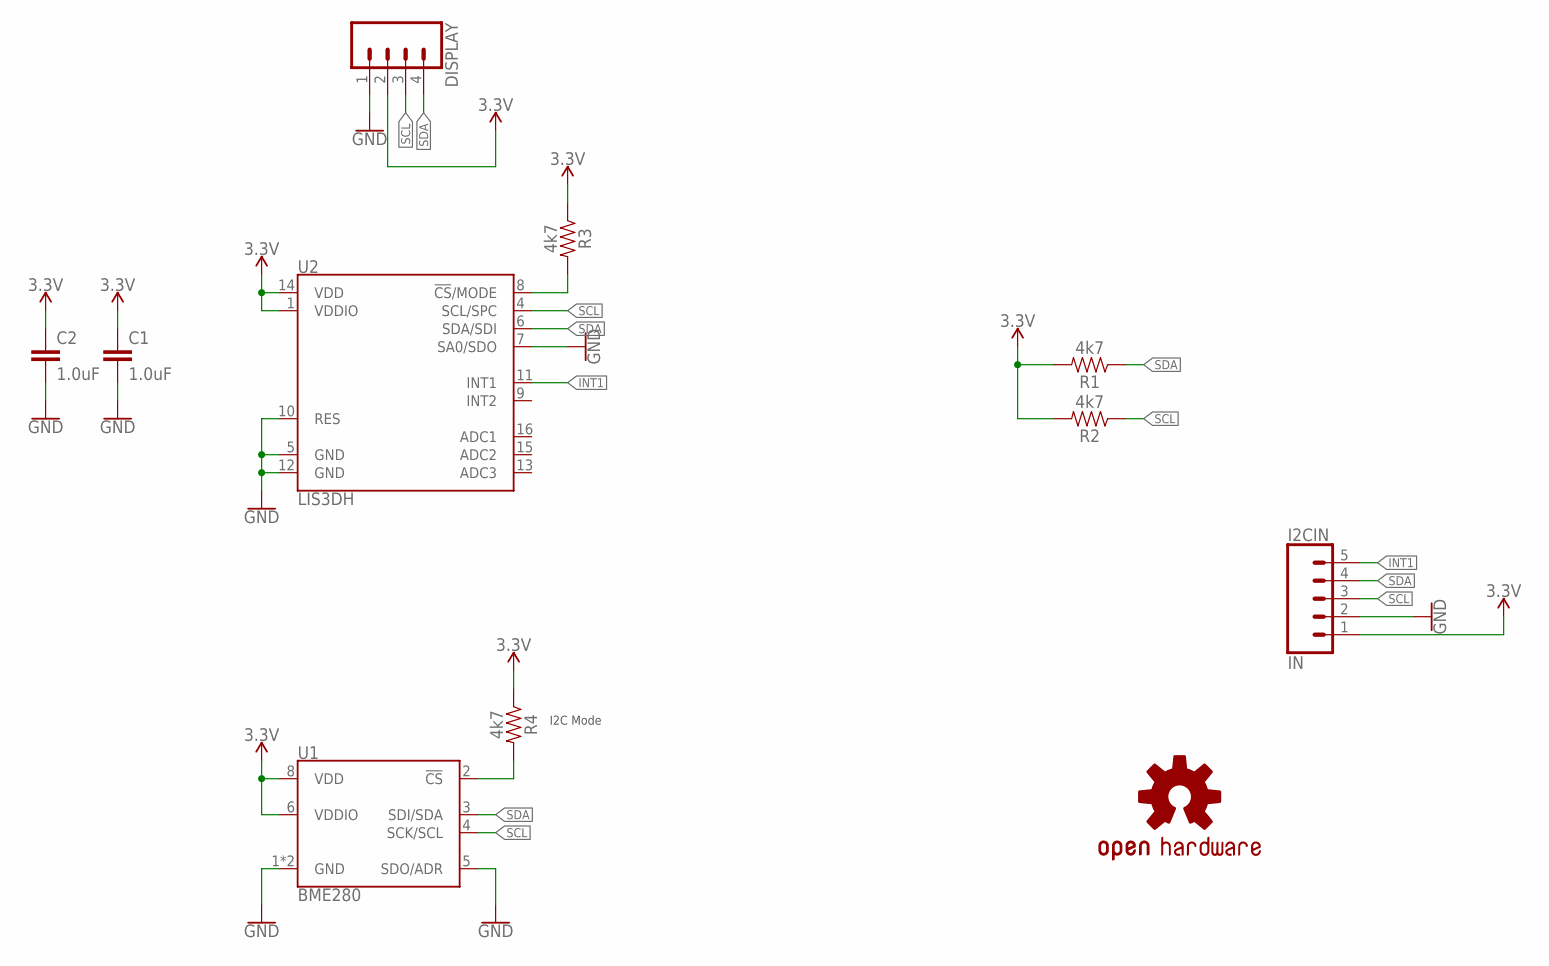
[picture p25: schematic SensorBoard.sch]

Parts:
C1, C2: 1.0uF; 0805
DISPLAY: CONN_04; 1X04
I2CIN: IN; 1X05
LOGO1: OSHW-LOGOL; OSHW-LOGO-L
R1, R2, R3, R4: 4k7; 0805
U1: BME280; LGA-8-2.5X2.5
U2: LIS3DH; LGA-16-3X3

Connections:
3.3V: C1.1, C2.1, DISPLAY.2, I2CIN.1, R1.2, R2.2, R3.1, R4.1, U1.6 (VDDIO), U1.8 (VDD), U2.1 (VDDIO), U2.14 (VDD)
GND: C1.2, C2.2, DISPLAY.1, I2CIN.2, U1.1 (GND), U1.5 (SDO/ADR), U1.7 (GND), U2.5 (GND), U2.7 (SA0/SDO), U2.10 (RES), U2.12 (GND)
INT1: I2CIN.5, U2.11 (INT1)
unnamed: R4.2, U1.2 (!CS)
unnamed: R3.2, U2.8 (!CS!/MODE)
SCL: DISPLAY.3, I2CIN.3, R2.1, U1.4 (SCK/SCL), U2.4 (SCL/SPC)
SDA: DISPLAY.4, I2CIN.4, R1.1, U1.3 (SDI/SDA), U2.6 (SDA/SDI)

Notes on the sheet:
I2C Mode

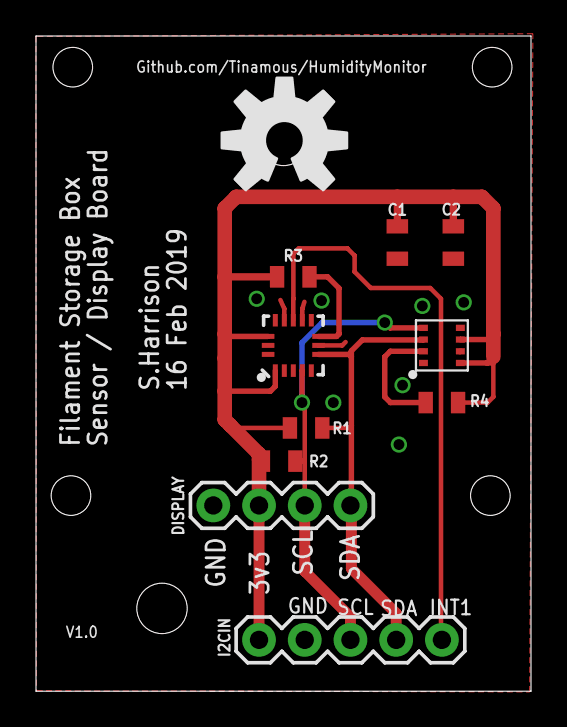
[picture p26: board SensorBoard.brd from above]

Board: 2 copper layers, 27.5 x 36.4 mm, 11 parts (0 on the bottom side), 7 nets.

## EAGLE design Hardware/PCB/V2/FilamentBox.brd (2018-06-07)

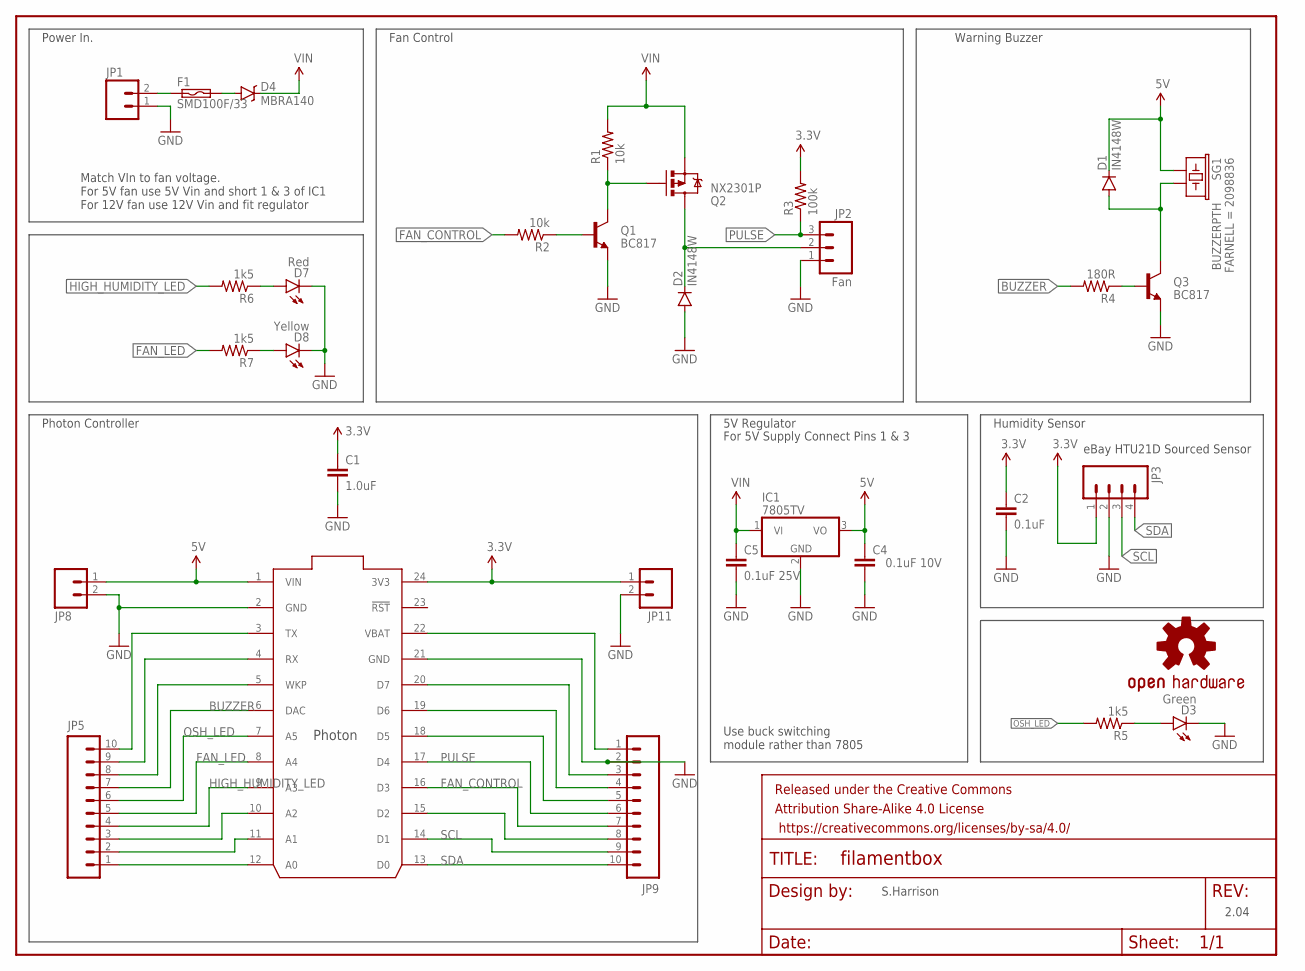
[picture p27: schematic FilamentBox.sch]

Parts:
C1: 1.0uF; 0805-CAP
C2: 0.1uF; 0805-CAP
C4: 0.1uF 10V; 0805-CAP
C5: 0.1uF 25V; 0805-CAP
D1, D2: IN4148W; SOD-123
D3: Green; LED-1206-BOTTOM
D4: MBRA140; SMA-DIODE
D7: Red; LED-1206-BOTTOM
D8: Yellow; LED-1206-BOTTOM
F1: SMD100F/33; SMD050F; MFGPART 2920L075DR; FARNELL 1822224
FRAME1: FRAME-LETTER; CREATIVE_COMMONS
IC1: 7805TV; TO220V
JP1: M02POLAR; MOLEX-1X2
JP2: Fan; MOLEX-1X3
JP3: M04PTH; 1X04
JP5, JP9: M10NO_SILK_PTH_FEMALE; 1X10_NO_SILK
JP8, JP11: M021X02_NO_SILK; 1X02_NO_SILK
LOGO1: OSHW-LOGOL; OSHW-LOGO-L
Q1, Q3: BC817; SOT23-BEC
Q2: NX2301P; SOT23-3
R1, R2: 10k; 0805
R3: 100k; 0805
R4: 180R; 0805
R5, R6, R7: 1k5; 0805
SG1: BUZZERPTH; BUZZER-12MM; FARNELL 2098836
U3: PHOTON

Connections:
3.3V: C1.1, C2.1, JP3.1, JP11.1, R3.2, U3.24 (3V3)
5V: C4.1, D1.C, IC1.3 (VO), JP8.1, SG1.+ (1), U3.1 (VIN)
BUZZER: JP5.7, R4.2, U3.6 (DAC)
FAN_CONTROL: JP9.7, R2.2, U3.16 (D3)
FAN_LED: JP5.5, R7.2, U3.8 (A4)
GND: C1.2, C2.2, C4.2, C5.2, D2.A, D3.C, D7.C, D8.C, IC1.2 (GND), JP1.1, JP2.1, JP3.2, JP8.2, JP9.2, JP11.2, Q1.E, Q3.E, U3.2 (GND), U3.21 (GND)
HIGH_HUMIDITY_LED: JP5.4, R6.2, U3.9 (A3)
unnamed: JP5.1, U3.12 (A0)
unnamed: Q1.C, Q2.1 (G), R1.1
unnamed: JP5.2, U3.11 (A1)
unnamed: Q1.B, R2.1
unnamed: JP5.3, U3.10 (A2)
unnamed: D2.C, JP2.2, Q2.3 (D)
unnamed: JP9.8, U3.15 (D2)
unnamed: JP5.8, U3.5 (WKP)
unnamed: JP5.9, U3.4 (RX)
unnamed: JP5.10, U3.3 (TX)
unnamed: Q3.B, R4.1
unnamed: D1.A, Q3.C, SG1.- (2)
unnamed: JP9.3, U3.20 (D7)
unnamed: JP9.1, U3.22 (VBAT)
unnamed: D3.A, R5.1
unnamed: F1.1, JP1.2
unnamed: D4.A, F1.2
unnamed: JP9.4, U3.19 (D6)
unnamed: JP9.5, U3.18 (D5)
unnamed: D7.A, R6.1
unnamed: D8.A, R7.1
OSH_LED: JP5.6, R5.2, U3.7 (A5)
PULSE: JP2.3, JP9.6, R3.1, U3.17 (D4)
SCL: JP3.3, JP9.9, U3.14 (D1)
SDA: JP3.4, JP9.10, U3.13 (D0)
VIN: C5.1, D4.C, IC1.1 (VI), Q2.2 (S), R1.2

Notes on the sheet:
5V Regulator
For 5V Supply Connect Pins 1 & 3
eBay HTU21D Sourced Sensor
Use buck switching module rather than 7805
Match VIn to fan voltage. For 5V fan use 5V Vin and short 1 & 3 of IC1 For 12V fan use 12V Vin and fit regulator
Power In.
Fan Control
Warning Buzzer
Photon Controller
Humidity Sensor
2.04
S.Harrison

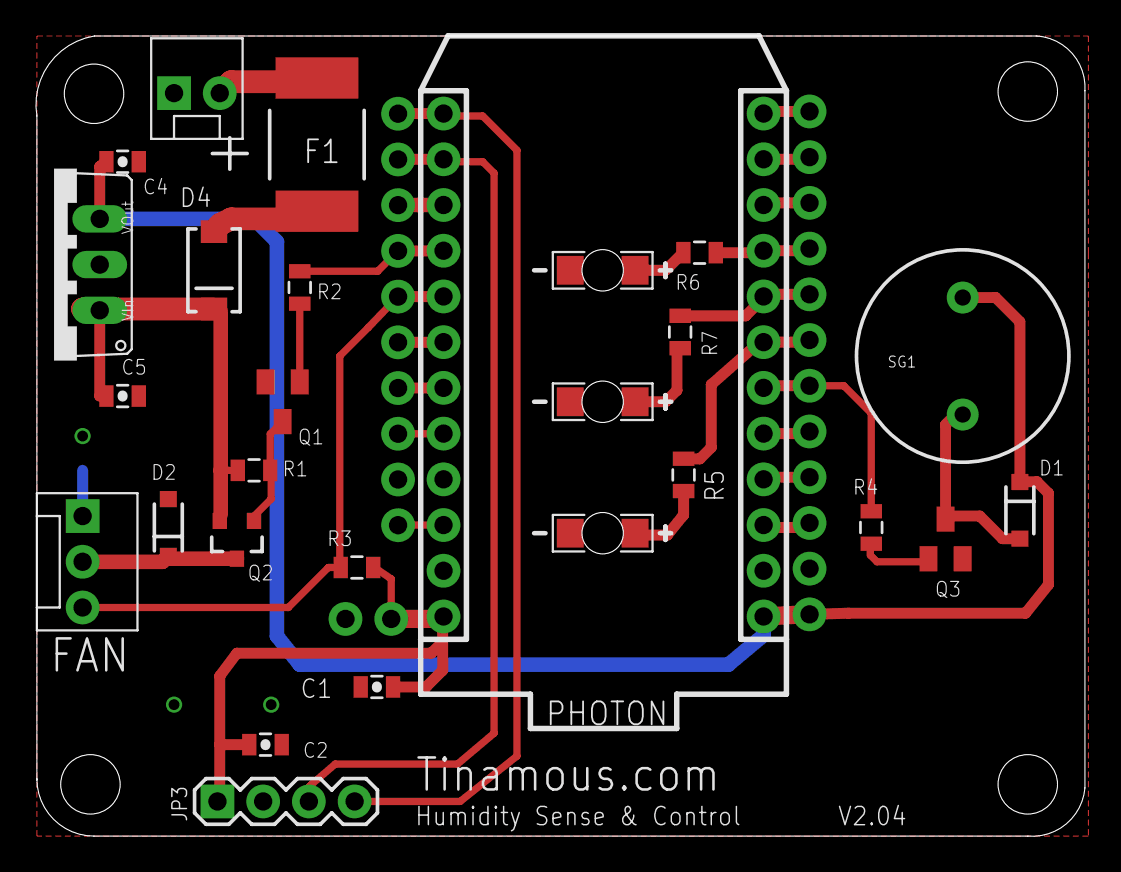
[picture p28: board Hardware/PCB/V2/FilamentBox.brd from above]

Board: 2 copper layers, 58.3 x 44.5 mm, 37 parts (1 on the bottom side), 33 nets.

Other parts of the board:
U$1, U$2, U$3, U$4: STAND-OFF

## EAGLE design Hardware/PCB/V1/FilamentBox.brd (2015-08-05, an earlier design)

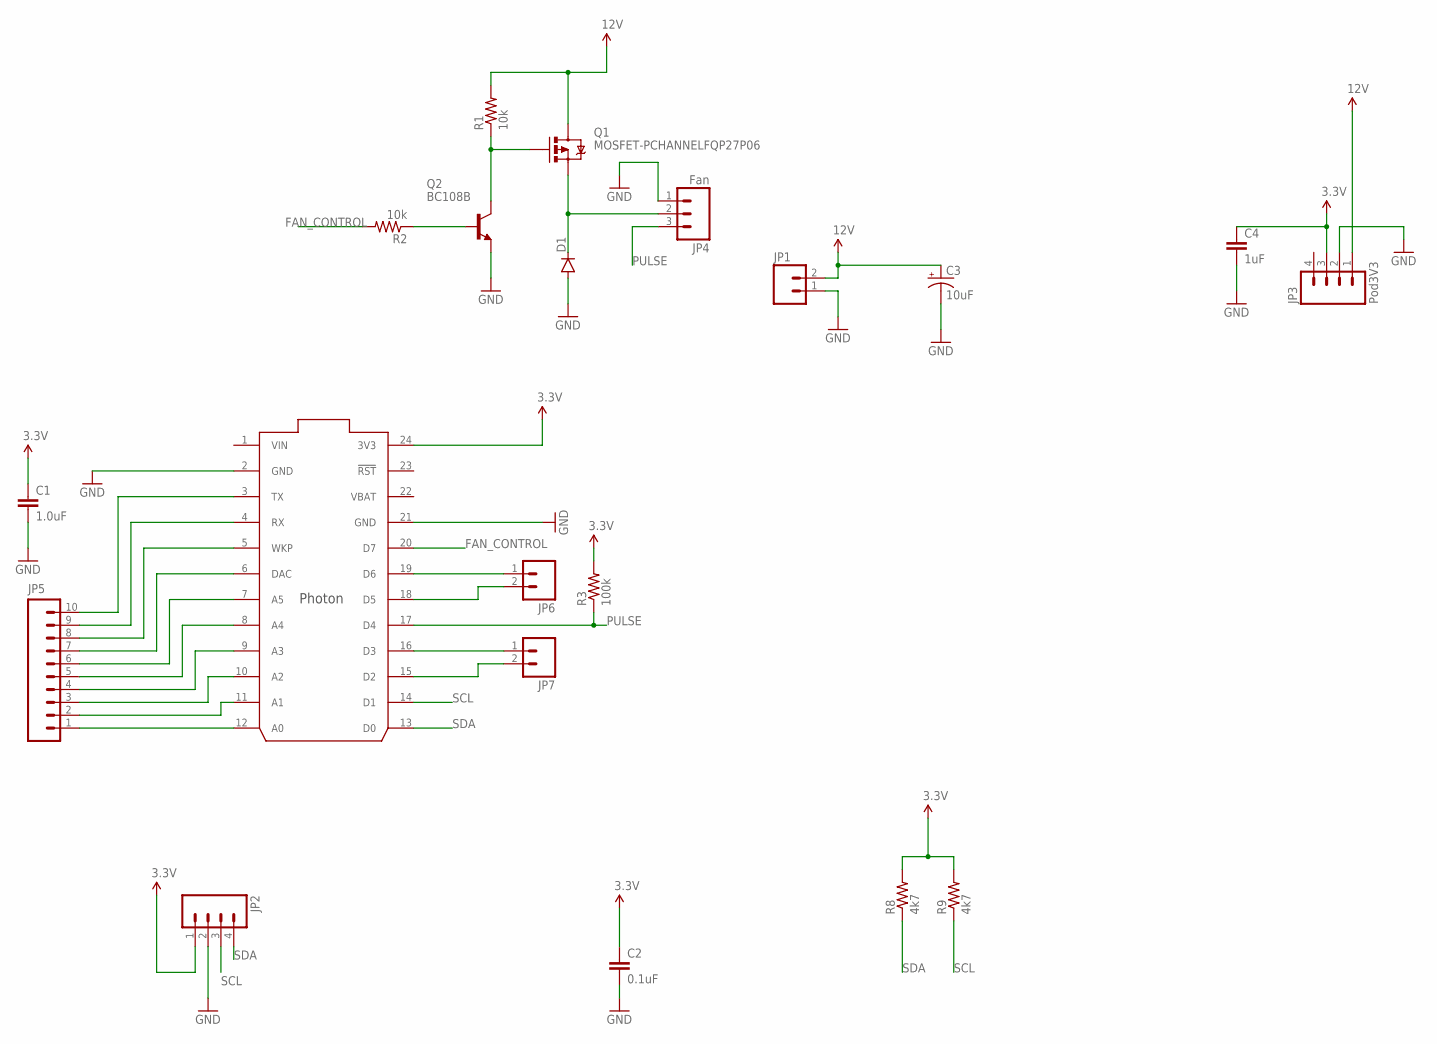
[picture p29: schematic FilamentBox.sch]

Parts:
C1: 1.0uF; 0805-CAP
C2: 0.1uF; 0805-CAP
C3: 10uF; CPOL-RADIAL-10UF-25V
C4: 1uF; 0805-CAP
D1: DIODESOD123; SOD-123
JP1: M02JST-PTH-2; JST-2-PTH
JP2: M04PTH; 1X04
JP3: Pod3V3; 1X04_NO_SILK_ALL_ROUND
JP4: Fan; MOLEX-1X3
JP5: M10NO_SILK_PTH_FEMALE; 1X10_NO_SILK
JP6, JP7: M021X02_NO_SILK; 1X02_NO_SILK
Q1: MOSFET-PCHANNELFQP27P06; TO220V
Q2: BC108B; TO18
R1, R2: 10k; 0805
R3: 100k; 0805
R8, R9: 4k7; 0805
U3: PHOTON

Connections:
3.3V: C1.1, C2.1, C4.1, JP2.1, JP3.3, R3.2, R8.2, R9.2, U3.24 (3V3)
12V: C3.1 (+), JP1.2, JP3.1, Q1.2 (D), R1.2
FAN_CONTROL: R2.2, U3.20 (D7)
GND: C1.2, C2.2, C3.2 (-), C4.2, D1.A, JP1.1, JP2.2, JP3.2, JP4.1, Q2.1 (E), U3.2 (GND), U3.21 (GND)
unnamed: JP5.1, U3.12 (A0)
unnamed: Q1.1 (G), Q2.3 (C), R1.1
unnamed: JP5.2, U3.11 (A1)
unnamed: Q2.2 (B), R2.1
unnamed: JP5.3, U3.10 (A2)
unnamed: D1.C, JP4.2, Q1.3 (S)
unnamed: JP5.4, U3.9 (A3)
unnamed: JP5.5, U3.8 (A4)
unnamed: JP5.6, U3.7 (A5)
unnamed: JP5.7, U3.6 (DAC)
unnamed: JP5.8, U3.5 (WKP)
unnamed: JP5.9, U3.4 (RX)
unnamed: JP5.10, U3.3 (TX)
unnamed: JP6.1, U3.19 (D6)
unnamed: JP6.2, U3.18 (D5)
unnamed: JP7.1, U3.16 (D3)
unnamed: JP7.2, U3.15 (D2)
PULSE: JP4.3, R3.1, U3.17 (D4)
SCL: JP2.3, R9.1, U3.14 (D1)
SDA: JP2.4, R8.1, U3.13 (D0)
VBAT: U3.22 (VBAT)
VIN: U3.1 (VIN)

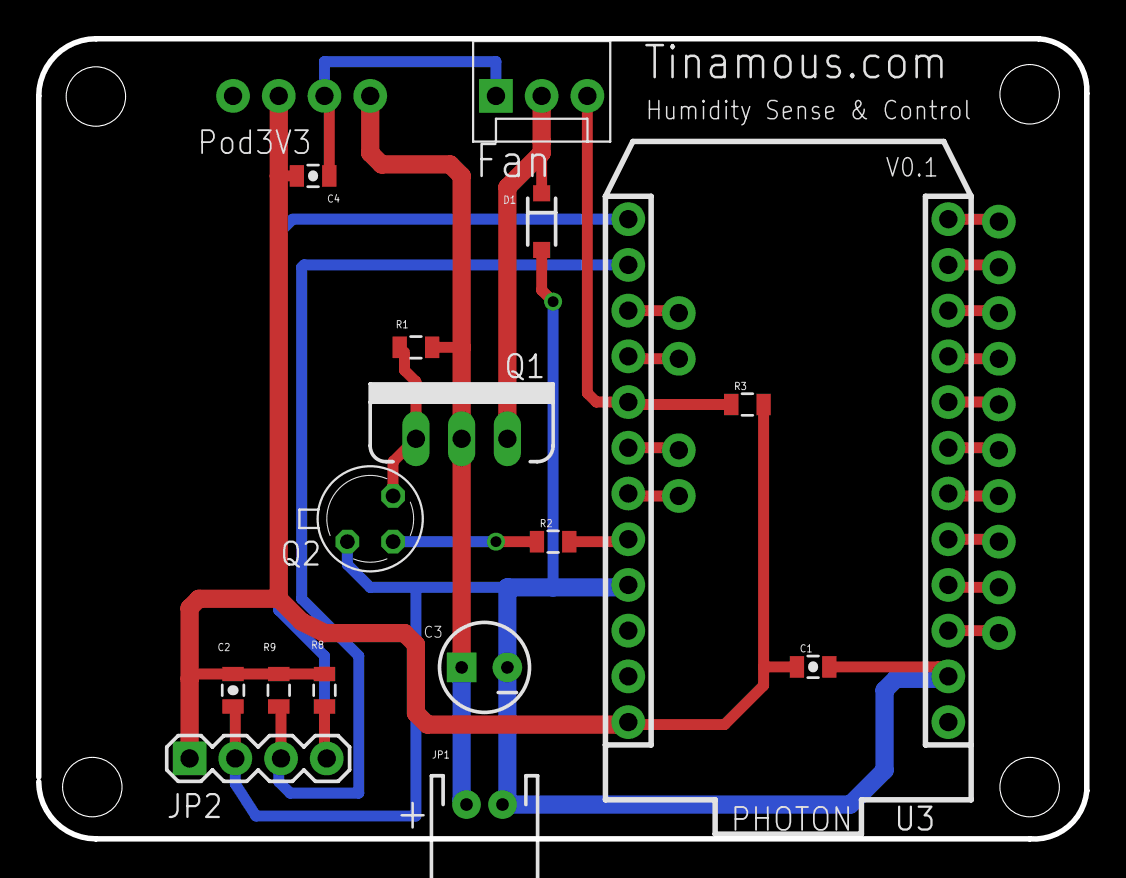
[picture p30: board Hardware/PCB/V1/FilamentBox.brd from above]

Board: 2 copper layers, 58.2 x 44.5 mm, 24 parts (0 on the bottom side), 24 nets.

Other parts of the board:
U$1, U$2, U$3, U$4: STAND-OFF

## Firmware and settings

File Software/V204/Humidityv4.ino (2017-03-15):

// This #include statement was automatically added by the Particle IDE.
#include <HTU21D.h>

// **********************************************************************
// Filament storage humidity monitor V2.04 PCB (Traffic lights version).
// **********************************************************************

int fanPulseIn = D4;
int fanControl  = D3;
int buzzer = DAC;
int highHumidityLed = A3;
int fanLed = A4;
int oshLed = A5;

// Temperature and humidity
HTU21D humiditySensor;

// Public exposed  variables for tracking humidity and temperature
double humidity = 0;
double temperature = 0;
int faultCode = 0;
int fanSpeed = 0; // percentage
int fanPulsesPerInterval = 0; // Non volatile int

// Public exposed methods
int setFanOnAt(String level);
int setWarnAt(String level);
int fanOn(String command);
int fanOff(String command);
int beep(String command);

// Default, run the fan when humidity > 20%
int fanOnAtHumidityLevel = 20;
int humidityWarningLevel = 30;

// Count of fan pulses
volatile int fanPulseCount = 0;

bool highHumidity = false;
int beepedCount =0;
int publishCount = 0;


void setup() {
    
    // First time deployment only
    // Address 0: Hardware version
    //EEPROM.write(0, 2);
    //EEPROM.write(1, fanOnAtHumidityLevel);
    //EEPROM.write(2, humidityWarningLevel);
    
    // Take control of the spark LED and make it dimmer as it's very
    // bright by default.
    RGB.control(true);
    RGB.brightness(100);
    
    // Set blue to show initializing.
    RGB.color(0, 0, 255);
    
    pinMode(fanPulseIn, INPUT_PULLUP);
    pinMode(fanControl, OUTPUT);
    pinMode(buzzer, OUTPUT);
    pinMode(highHumidityLed, OUTPUT);
    pinMode(fanLed, OUTPUT);
    pinMode(oshLed, OUTPUT);
    
    digitalWrite(fanControl, LOW);
    digitalWrite(buzzer, LOW);
    digitalWrite(highHumidityLed, HIGH);
    digitalWrite(fanLed, HIGH);
    digitalWrite(oshLed, HIGH);
    
    // Load in the settings
    fanOnAtHumidityLevel = EEPROM.read(1);
    if (fanOnAtHumidityLevel == 0xFF) {
        fanOnAtHumidityLevel = 20;
    }
    
    humidityWarningLevel = EEPROM.read(2);
    if (humidityWarningLevel == 0xFF) {
        humidityWarningLevel = 30;
    }
    Particle.publish("Status", "Setting FanOn at: " + String(fanOnAtHumidityLevel) + "%, WarnAt: " + String(humidityWarningLevel) + "%");
    delay(1000);
    
    // Setup I2C as master.
    // Appears bug in Particle where CLOCK_SPEED_400KHZ is undefiend.
    // Works with Core but not Photon.
    // For now default to 100KHZ which appears to work for the DTH21 anyway
    // Wire.setSpeed(CLOCK_SPEED_400KHZ);
    Wire.begin();
    
    // Initialize Temperature and humidity
    if (!humiditySensor.begin()) {
        RGB.color(255, 0, 00);
        Particle.publish("Status", "Humidity Sensor setup failed.");
        delay(2000);
    }
      
    Particle.variable("humidity", &humidity, DOUBLE);
    Particle.variable("temperature", &temperature, DOUBLE);
    Particle.variable("faultCode", &faultCode, INT);
    Particle.variable("fanPulses", &fanPulsesPerInterval, INT);
    Particle.variable("fanOnAt", &fanOnAtHumidityLevel, INT);
    Particle.variable("warnAt", &humidityWarningLevel, INT);
    
    // register the cloud function
    Particle.function("setFanOnAt", setFanOnAt);
    Particle.function("setWarnAt", setWarnAt);
    Particle.function("fanOn", fanOn);
    Particle.function("fanOff", fanOff);
    Particle.function("beep", beep);
    
    attachInterrupt(fanPulseIn, fanPulse, FALLING);
    
    doBeep(2);
    Particle.publish("Status", "Setup complete. V4.1.1");
    RGB.color(0, 0, 0);
    delay(250);
}

void loop() {
    
    // Indicate blue for reading.
    RGB.color(0, 0, 255);
    
    // Reset the fault code before measuring.
    faultCode = 0;
    
    // Read measurements
    readHumidity();
    readTemperature();
    
    // Update control/output based on measurements
    updateFanControl();
    setLedForHumidityLevel();
    beepIfNeeded();
    updateTinamous();
    
    // Store the fan pulses during this loop
    fanPulsesPerInterval = fanPulseCount;
    fanPulseCount = 0;
    
    delay(10000);
} 

void updateTinamous() {
    // Only publish the 
    if (humidity > humidityWarningLevel && !highHumidity) {
        highHumidity = true;
        Particle.publish("Status", "High Humidity. Fan will not be run at this level.");
    }
    
    if (humidity < fanOnAtHumidityLevel) {
        highHumidity = false;
    }
    
    // Every minute.
    if (publishCount >= 0) {
        Particle.publish("senml", "{'e': [{'n':'Humidity', 'v':" + String(humidity) + "},{'n':'temperature','v':" + String(temperature) + "}]}");
        publishCount = 0;
    }
    publishCount++;
}


void setLedForHumidityLevel() {

    digitalWrite(highHumidityLed, LOW);
    digitalWrite(oshLed, LOW);
    
    // If > 30, Red - very high humidity
    // if > 20, higher than wanted
    // Otherwise Green - all is well...
    if (humidity > humidityWarningLevel) {
        RGB.color(255, 0, 0);
        RGB.brightness(100);
        digitalWrite(highHumidityLed, HIGH);
    } else if (humidity > 20) {
        RGB.color(255, 255, 0);
        RGB.brightness(100);
        digitalWrite(highHumidityLed, HIGH);
    } else {
        RGB.color(0, 255, 0);
        RGB.brightness(50);
        digitalWrite(oshLed, HIGH);
    }
}

void readHumidity() {
    float h = humiditySensor.readHumidity();
    if (h < 100) {
        humidity = (double)h;
    } else {
        faultCode = h;
    }
}

void readTemperature() {
    float t = humiditySensor.readTemperature();
    if (t<100) {
        temperature = (double)t;
    } else {
        faultCode = t;
    }
}

void updateFanControl() {
    // Use the global fanSpeed variable.
    
    int newFanOnCount = fanSpeed;
   
    if (humidity > humidityWarningLevel ) {
        // If measured humidity is above 30 (humidityWarningLevel) then
        // don't run the fan as the unit is most likely in free air
        // and this will ruin the silica gel quickly.
        newFanOnCount = 0;
        
        // The humidity will gradually drop once the unit is in a controlled environment
        // and then the fan can resume 
        Particle.publish("Status", "Humidity (" + String(humidity) + ")> " + String(humidityWarningLevel) + "%. Stopping fan to prevent saturating gel");
    } else if (humidity > fanOnAtHumidityLevel) {
        // humidity is higher than we would like. Between fanOnAt and humidityWarningLevel
        // switch the fan on for n-minutes
        newFanOnCount = 6;
    } else  {
        // Humidity is below the level required to need the fan to run
        // so do nothiung.
    }
    
    // Every good cycle causes count to be decremented. When 0 or less fan is switched off.
    // 10 mins off, 20 seconds on.
    if (newFanOnCount < -60) {
        Spark.publish("Status", "Running fan for general air refresh");
        newFanOnCount = 2;
    }
    
    setFan(newFanOnCount);
    
    // decrease the number of itterations the fan needs to be on for.
    newFanOnCount--; 
}

void beepIfNeeded() {
    // Beep a max of n-times when the humidity goes out of range
    // Once it's back in range reset the counter.
    if (humidity > humidityWarningLevel) {
        if (beepedCount<5) {
            doBeep(5);
            beepedCount++;
        } else {
            /// Silent beep beep beep to stop it being annoying
        }
    } else {
        beepedCount = 0;
    }
}

// Particle Method
int setFanOnAt(String level) {
    // This relies on level being a single numeric value.
    fanOnAtHumidityLevel = level.toInt();
    EEPROM.write(1, fanOnAtHumidityLevel);
    Particle.publish("Status", "Setting fan trigger humidity level at: " + String(fanOnAtHumidityLevel) + "%");
    return fanOnAtHumidityLevel;
}

int setWarnAt(String level) {
    humidityWarningLevel = level.toInt();
    EEPROM.write(2, humidityWarningLevel);
    Particle.publish("Status", "Setting humidity waring level at: " + String(humidityWarningLevel) + "%");
    return humidityWarningLevel;
}

// Particle Method
int fanOn(String command)
{
    Particle.publish("Status", "Switching fan on for 10 minuites.");
    // On for 10 mins (6 itterations per min)
    setFan(10 * 6);
    return 10*6;
}

// Particle Method
int fanOff(String command)
{
    Particle.publish("Status", "Switching fan off.");
    
    // On for 0 itterations
    setFan(0);
    return 0;
}

int beep(String command)
{
    doBeep(command.toInt());
    return 0;
}

// Use the number of cycles that the fan should be on for.
void setFan(int fanCount) {
    
    int newfanSpeed = fanCount; //max(speed, fanOverrideSpeed);
    
    // Store in the Particle variable
    fanSpeed = newfanSpeed;
    
    // TODO: Use AnalogWrite when fan connected to it.
    if (fanSpeed > 0) {
        digitalWrite(fanControl, HIGH);
        digitalWrite(fanLed, HIGH);
    } else {
        digitalWrite(fanControl, LOW);
        digitalWrite(fanLed, LOW);
    }
}

// Beep to indicate a problem (and flash the red LED)
void doBeep(int count) {
    for(int i=0; i<count; i++) {
        digitalWrite(highHumidityLed, LOW);
        for(int j=0; j<150; j++) {
            digitalWrite(buzzer, HIGH);
            delay(1);
            digitalWrite(buzzer, LOW);
            delay(1);
        }
        delay(100);
        digitalWrite(highHumidityLed, HIGH);
        delay(100);
    }
    Particle.publish("Status", "Beep, Beep, Beep...");
}

void fanPulse() {
    fanPulseCount++;
}

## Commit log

2015-07-21 Initial commit of Particle Core/Photon powered Temperature and Humidity meter.
2015-08-05 Added latest 3D models, laser cutter design for partitiona and Photon based humidity monitor PCB
    [FilamentBox.brd, FilamentBox.sch, HumidityCase.scad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]
2015-08-05 Updated with fan monitor and control.
    Increased loop delay to 15s so a measurement happens every 15s
2015-08-05 Made padding fixed 5mm width so that they print quicker and can be stacked to fill excess width allowing a better tollerance.
    [HumidityRodPadding.scad, HumidityRodPadding.stl]
2016-02-03 Adding PCB files for V1 (0.1) and V2 (0.2) boards.
    [FilamentBox.brd, FilamentBox.sch]
2016-02-03 Minor display update for PCB and added eagle project file.
    [FilamentBox.brd]
2016-02-03 Removed PCB files from Case folder.
    [FilamentBox.brd, FilamentBox.sch]
2016-02-03 Removed unused 3D printed parts.
    [HumidityCase.scad, HumidityCase.stl, HumidityCaseLid.scad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]
2016-02-03 Remove partition file as this is for a different design of case.
    [PartitionWithFill.dxf]
2016-02-03 Updated to latest laser cut acrylic plans.
    [FanInsert-V2.02.dxf]
2016-02-03 Added 3D printed funnel designs used to pour silica gel in.
    [Funnel.scad, Funnel.stl, Funnel2.scad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]
2016-02-03 Updated source code to latest version to work with V2 (0.2) boards.
    Remopved lots of noisy publishing used during debug.
2016-02-03 Added instructions for replacing the silica gel and details on mounting holes.
2016-02-03 Added bill of materials.
    [BOM.xlsx]
2016-02-03 Added Silica Gel to BOM (It's kind of important!) and price for PCB.
    [BOM.xlsx]
2016-02-03 Updated BOM
    Added cutting dxf for laser cutting the acrylic case.
    [BOM.xlsx, Sheet-1-V2.02 - Cutting.dxf]
2017-01-03 Update (to 2.04)- Added reverse mount LEDs (Red, Yellow and Green for Humidity warning, fan status and OK (with OSH Logo)). Added poly fuse and diode for input protection. Swapped orientation of VIn 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
    Sent to DirtyPCBs (3-Jan-2017)
    [FilamentBox.brd, FilamentBox.sch]
2017-01-03 Added Funnel3, an improved design for pouring silica gel into the acrylic case.
    [Funnel3.scad, Funnel3.stl]
2017-01-03 Added files for the "mini" gel box - a self contained gel box - didn't work so well as it really needs air pushed through it
    [SilicaGelCase.scad, SilicaGelCase.stl, SilicaGelCaseLid.scad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]
2017-03-15 Added media for V2.04 PCB and some assembly
2017-03-15 Added firmware for the V2.04 PCB
2018-06-07 Added part values
    [FilamentBox.brd, FilamentBox.sch]
2018-06-07 Updated export images of PCB/Schematic
2018-06-26 Added PiHanle 3D printed handle.
    [PiHandle.stl]
2019-02-16 I2C Display adaptor and sensor board. Connects to I2C 4 pin connector on main board in place of HTU21D.
    Adds BME280, LIS3DH and I2C connector for 0.96" displays.
    [SensorBoard.GBL, SensorBoard.GBO, SensorBoard.GBP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]
2019-02-16 Big handles for box to make opening the lid easier.
    [Handle3-ABS.stl, Handle3-Makespace.stl, Handle3-PLA.stl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]
2019-02-16 0.96" Blue display holder and PCB mouont for main PCB.
    [ScreehHolder2-4.stl]

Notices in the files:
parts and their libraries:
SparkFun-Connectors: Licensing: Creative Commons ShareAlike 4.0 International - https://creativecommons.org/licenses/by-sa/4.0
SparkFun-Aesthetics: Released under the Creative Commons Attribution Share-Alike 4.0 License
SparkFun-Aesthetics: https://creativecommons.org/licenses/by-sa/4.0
